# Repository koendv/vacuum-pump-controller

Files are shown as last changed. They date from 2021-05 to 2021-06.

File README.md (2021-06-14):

# vacuum pump controller

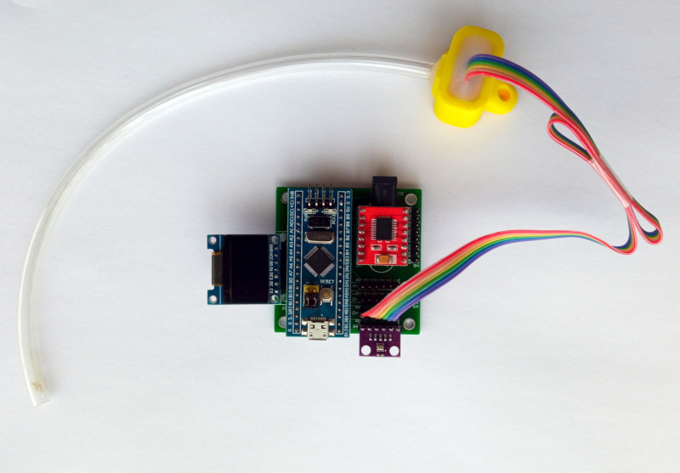
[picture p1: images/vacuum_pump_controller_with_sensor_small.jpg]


This is a controller for a vacuum pump, useful in pick-and-place machines. The controller adjusts the rpm of a vacuum pump to maintain a constant vacuum. The controller can be used over usb, as part of a pick-and-place machine, or standalone, with a footswitch.

## Features:

- PID controller with autotuning

- controls one 12V 1A vacuum pump (diaphragm pump).

- up to 4 x BMP280 pressure sensors: 1 for outside pressure, 1 for vacuum pressure, and 2 for two pick-and-place nozzles. The pressure sensors on the nozzles are used to check whether a component has been picked up or fallen off.

- sensor pressure range 300 to 1100 hPa

- up to 2 x 12V solenoid valves, for up to two pick-and-place nozzles.

## Usage

The controller needs two power sources: +5V from the usb connector for the electronics, and +12V from the DC jack for the vacuum pump and solenoid valves.

Plug the controller in a usb port, and connect to the usb serial port. On linux, this is ``minicom -D /dev/ttyACM0``

Hit the reset button to see the boot message:

```
vacuum controller - type h for help
sensors ok  ok  -  -
ready
>
```
The ``sensors`` line indicates sensor status:

- ``ok`` sensor detected and running
- ``-`` no sensor detected
- ``?`` bmp280 unresponsive, or sensor is wrong type (not bmp280)

Every command is briefly described.

#### h - Help

 ``h`` *help* prints a command summary:

```
>h
commands, ## = int, #.## = float:
? print status
s#.## setpoint
p#.## proportional gain
i#.## integral gain
d#.## derivative gain
o#.## manual mode
a autotune
l## logging on/off
m## m-code
v## valve on/off
w write settings
r reset
f firmware
h help
>
```

All commands are a single character, optionally followed by a number, and terminated with *enter*.

#### ? - print status

```
>?
vacuum hPa: 99.97 motor: 73.60% mode: auto
setpoint hPa: 100.00 Kp: 150.00 Ki: 50.00 Kd: 0.00 logging: 0
pressure hPa: 938.86 838.89 939.41 0.00
sensors ok  ok  ok  -
```
In this example, the boot message shows there are three sensors. The first sensor measures atmospheric pressure; the second sensor measures the pressure in the vacuum vat; the third measures the pressure at the nozzle. In this example the fourth sensor is absent (-).

The vacuum is the difference between the first and the second sensor. All pressures are in hPa. Atmospheric pressure is around 1000 hPa.

*vacuum* is the PID controller measured value. *motor* is PWM, in percent. *mode* is *auto* when the PID controller sets motor PWM. *mode* is *manual* if motor PWM has been set using the ``o`` command.

The vacuum pump controller is a PID controller. *setpoint* is the
desired value; *Kp*, *Ki* and *Kd* are controller proportional, integral and derivative gain. It is normal for *Kd* to be zero. If *logging* is non-zero, pressure is logged on the console every 0.1s.

*pressure* is the pressure from the four sensors, in hPa. If a sensor is not plugged in, the pressure is 0.

*sensors* is the sensor state. If a sensor says ``?``, check the cable, check the sensor is plugged in right, or try power cycling.

#### s - Setpoint

The *setpoint* command sets the desired vacuum, in hPa.
```
>s100.0
ok
```

#### p - Proportional Gain

Sets the PID controller Kp.
```
>p150.0
ok
```

#### i - Integral Gain

Sets the PID controller Ki.
```
>i50.0
ok
```

#### d - Derivative Gain

Sets the PID controller Kd. Usually zero.

```
>d0
ok
```

#### l - Logging

Switches logging on or off.

- ``l0`` logging off.
- ``l1`` logging on.

Use the ``w`` command if you want this and other settings to be saved.

When logging is on, every sample is printed on the console output, in one line, e.g.:
```
;1743075;52417;93876;83764;93926;0;2067058
```
The fields are:
- time since boot in milliseconds
- motor PWM; a value from 0 to 65535.
- pressure of sensor 1, 2, 3, 4 in Pa.
- a checksum that is the 32 bit sum of the 6 previous numbers.

Logging output can be imported in a spreadsheet as [csv](https://en.wikipedia.org/wiki/Comma-separated_values). The line begins with a semi-colon ";", and numbers are separated by a semi-colon. If you parse console output, check for lines that begin with a semi-colon.

#### v - Valve

Switches outputs BO1 and BO2 on/off. These outputs are normally connected to solenoid valves.

- ``v00`` switch BO1 off
- ``v01`` switch BO1 on
- ``v10`` switch BO2 off
- ``v11`` switch BO2 on

*Restriction*: Because of the way the driver ic works, both solenoid valves can not be powered at the same time. Switching one solenoid valve on automatically switches off the other.

#### o - manual Output

Sets the motor PWM manually. Value is a number from 0 to 100, inclusive.

- ``o100`` full speed
- ``o0`` stop. mnemonic: *output zero*
- ``o`` return to automatic mode

#### a - Autotune

*Autotune* measures the step response. Values for Kp, Ki and Kd are calculated from the step response using [lambda tuning](https://www.controleng.com/articles/fundamentals-of-lambda-tuning/). Running *autotune* optimizes controller response time, and the accuracy with which the vacuum is maintained.

```
>a
autotune - press c to cancel
cycle 1/5
  0%    0 hPa
 11%    1 hPa
100%  131 hPa
  0%    0 hPa
100%   83 hPa
minpwm: 7141 maxpwm: 65535 minpressure: 0.49 maxpressure: 130.83
tau: 2.69s Kp: 149.34 Ki: 55.54
...
Kp: 149.60 Ki: 54.03 Kd: 0.00
enter w to save
```

After *autotune*, if the calculated settings seem correct, use ``w`` to store these settings in non-volatile memory. If you choose not to save, the old settings will be restored after the next reset or power cycle.

To adjust the controller to your system, *you need to run autotune* ``a`` *and save the settings* ``w`` *at least once.* Without autotune, controller response will be sluggish.

Run *autotune* again if firmware has been updated, vacuum pump or vacuum vessel has changed.

#### m - M-Code

M-code commands consist of the letter ``M`` followed by a three-digit number. M-code commands are not echoed back when you type them, and no ``>`` prompt is printed when the command is finished. See the section on [OpenPnP](#openpnp) for details.

#### w - Write
The ``w`` write command saves Kp, Ki, Kd, setpoint, and logging to non-volatile memory. The saved values will be restored on power-up.

```
>w
ok
```

#### r - Reset
The ``r`` reset command reboots the controller.

```
>r
vacuum controller - type h for help
sensors ok  ok  ok  -
ready
>
```

#### f - Firmware
The ``f`` command prints firmware version, system uptime, memory and cpu statistics:

```
>f
compiled Jun  1 2021
up 0:16
11240 bytes free
11 ms slowest loop
>
```

Use this to check for reboots, memory leaks, and cpu hogs.

### Connections

Connect pressure sensors, vacuum pump, and solenoid valve.

#### Sensors

Up to 4 BMP280 boards can be connected in headers H1..H4.

- H1: air pressure
- H2: pressure inside vacuum vessel
- H3: optional, pressure at nozzle 1
- H4: optional, pressure at nozzle 2

The minimal configuration is sensors at H1 and H2.
BMP280 sensors measure pressures from 300 hPa to 1100 hPa.

#### Calibration

There is no need to calibrate the sensors; the sensors are calibrated at the factory.

#### Vacuum Pump
 Connect a 12V DC brushless vacuum pump. Maximum current of the TB6612 driver is 1A continuous.

 If the vacuum pump has two wires:

 - red (+) to AO1
 - black (-) to GND

The  vacuum pump is limited to 12V 1A.

For 12V pumps that draw more than 1A, see [pumps with PWM input](README_DEVELOPER.md#pumps-with-pwm-input)

For the controller to work, if the voltage on pin AOUT1 increases, the vacuum pump should run faster, and the vacuum should increase.

#### Solenoid valve

Connect the first solenoid valve:

 - red (+) to B01
 - black (-) to GND

If there is a second solenoid valve, connect:

 - red (+) to B02
 - black (-) to GND

### Footswitch

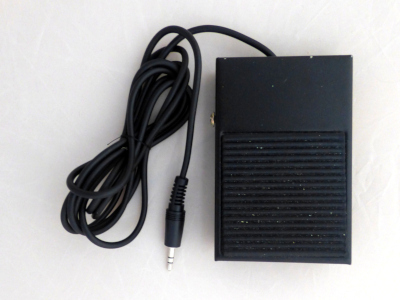
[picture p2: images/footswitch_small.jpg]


Sometimes a small, standalone tool is preferred. The optional footswitch can be used to switch the first solenoid valve on and off.

The footswitch connects using a 3.5mm TRRS jack. Solder a cable from an old mobile phone earset to an [SPDT footswitch](https://www.aliexpress.com/wholesale?SearchText=footswitch&SortType=price_asc). Connections are:

- Tip: NO Normally open
- Ring1: NC Normally closed
- Ring2: unused
- Shield: Common

The console prints ``footswitch`` when a footswitch is detected.

In standalone mode connect the usb port to a mobile phone charger.

## Display

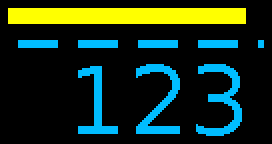
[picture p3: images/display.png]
oled


The display is a yellow/blue oled display, 128x64, SPI, SSD1306 controller. The display is optional; the controller also works without display. The display shows pump, sensors, and vacuum:

- The bargraph at the top shows the pump motor. The larger the bar graph, the harder the motor works.

- Next up to four rectangles, one for each sensor that is plugged in. If the rectangle is blue, the sensor is ok; if the rectangle is yellow there is a problem.

- At the bottom the vacuum in hPa. The vacuum is the difference between the first and the second sensor.

To the right there is a small square that blinks slowly to show the display works.

## Configuration
### linux

On linux, configure udev. As root:

```
cat <<EOD > /etc/udev/rules.d/98-vacuum_pump.rules
ATTRS{idProduct}=="5740", ATTRS{idVendor}=="0483", ENV{ID_MODEL}=="vacuum_pump", MODE="664", GROUP="dialout", ENV{ID_MM_DEVICE_IGNORE}="1"
SUBSYSTEM=="tty", ACTION=="add", ENV{ID_MODEL}=="vacuum_pump", SYMLINK+="ttyACM99_vacuum_pump"
EOD
chmod 644 /etc/udev/rules.d/98-vacuum_pump.rules
udevadm control --reload-rules
```
This creates a device ``/dev/ttyACM99_vacuum_pump``, open to everybody in the *dialout* group. Add yourself to the dialout group:
```
sudo adduser "$USER" dialout
```
Unplug and plug in the vacuum pump controller. Check ``dmesg`` shows a new usb device *vacuum pump*. Check ``minicom -D /dev/ttyACM99_vacuum_pump`` gives you the console prompt of the vacuum pump.

### OpenPnP

*TBD - in progress*

[OpenPnP](https://openpnp.org/) is software to run a machine that puts electronic components on a printed circuit board for soldering (pick-and-place machine).
Typically, a pick-and-place machine uses vacuum to pick up small components.
OpenPnP accesses the vacuum pump controller using the OpenPnP GCodeDriver.

OpenPnP uses M-code M115 to detect a controller.

The m-codes for vacuum have the structure ``M8`` *index* *action*, with *index*:

- 0: ambient air (read only)
- 1: vacuum pump
- 2: nozzle1
- 3: nozzle2

and *action*:

- 0: switch off
- 1: switch on
- 2: read absolute pressure in hPa
- 3: read vacuum in hPa

The following m-codes are available for easy integration with [openpnp](http://openpnp.org):

| code | description |
| ---- | --- |
| M115 | firmware version |
| M800 | no-op |
| M801 | no-op |
| M802 | read absolute air pressure |
| M803 | always reads 0 |
| M810 | switch pump off |
| M811 | switch pump on |
| M812 | read absolute pressure at pump |
| M813 | read vacuum at pump |
| M820 | switch nozzle 1 solenoid off |
| M821 | switch nozzle 1 solenoid on |
| M822 | read absolute pressure at nozzle1 |
| M823 | read vacuum at nozzle1 |
| M830 | switch nozzle 2 solenoid off |
| M831 | switch nozzle 2 solenoid on |
| M832 | read absolute pressure at nozzle2 |
| M833 | read vacuum at nozzle2 |

Example:
Switch pump on.

```
m811
ok
```
Measure absolute air pressure and absolute pump pressure:

```
m802
[read:937]
ok
m812
[read:837]
ok
```
Vacuum is difference between air pressure and pump pressure:

```
m813
[read:100]
ok
```

Vacuum values can be negative due to small measurement errors, or if the sensor for measuring atmospheric pressure is missing.

In OpenPnP, configure a GCodeDriver VACUUM_PUMP for serial port ``/dev/ttyACM99_vacuum_pump``.

Setting|value
---|---
FIRMWARE_NAME|vacuum pump
COMMAND_CONFIRM_REGEX|^ok$
COMMAND_ERROR_REGEX|^(what\\?\|how\\?)$
ACTUATE_BOOLEAN_COMMAND|M8\{Index\}\{True:1\}\{False:0\}
ACTUATOR_READ_COMMAND|M8\{Index\}3
ACTUATOR_READ_REGEX|\\[read:(?<Value>-?\d+)\\]

For head, nozzle 1 and nozzle 2, use three VACUUM_PUMP actuators with index:

Actuator|Index
---|---
head|1
nozzle 1|2
nozzle 2|3

See [machine.xml](openpnp/machine.xml)

## Hardware

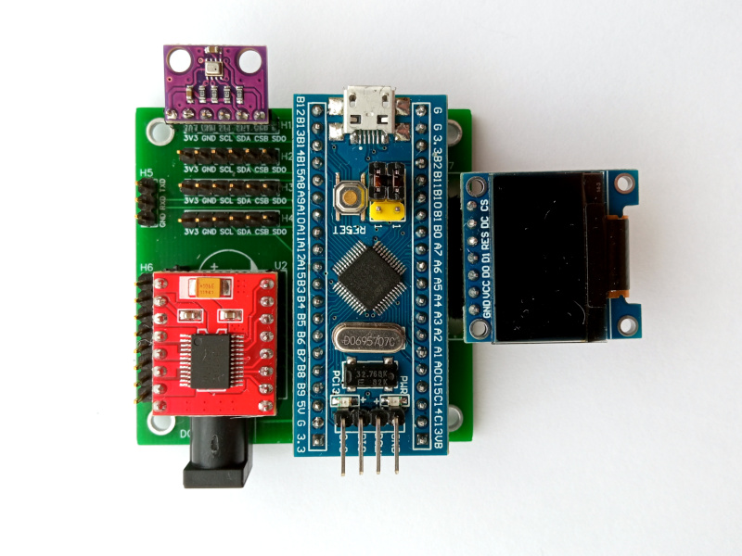
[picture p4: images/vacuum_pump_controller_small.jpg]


The board is built around an STM32F103 *Blue Pill*. The microcontroller reads the pressure from the BMP280 sensors, runs a PID controller algorithm, and sets PWM on a TB6612FNG driver to control the speed of the vacuum pump.

- [schematic](doc/schematic.pdf)
- [pcb top](doc/pcb_top.pdf)
- [pcb bottom](doc/pcb_bottom.pdf)
- [easyeda/oshw project](https://oshwlab.com/koendv/vacuum-pump-controller).

The board is 2 layer, 55 x 55 mm, hand-solderable.

### Bill of Materials

Off-the-shelf parts:

|  #  | description |
| --- | --- |
| 1 | [STM32F103xx](https://www.aliexpress.com/item/32525208361.html) controller board, 128kbyte flash. |
| 4 | [BMP280 3.3V pressure sensor "GY-BMP280-3.3"](https://www.aliexpress.com/item/4000587263474.html) |
| 1 | [TB6612FNG dual motor driver](https://www.aliexpress.com/item/32978024026.html) |
| 1 | [OLED 128x64, SPI, 7pin, SSD1306, yellow/blue](https://www.aliexpress.com/item/32638662748.html)  |
| 1 | DC005 DC jack |
| 1 | PJ-320A 3.5 mm audio jack, 4 pin, through-hole |
| 1 | 47u/25V capacitor |

FDM 3D-printed parts:

- 3 x pressure sensor housing

## Sensors

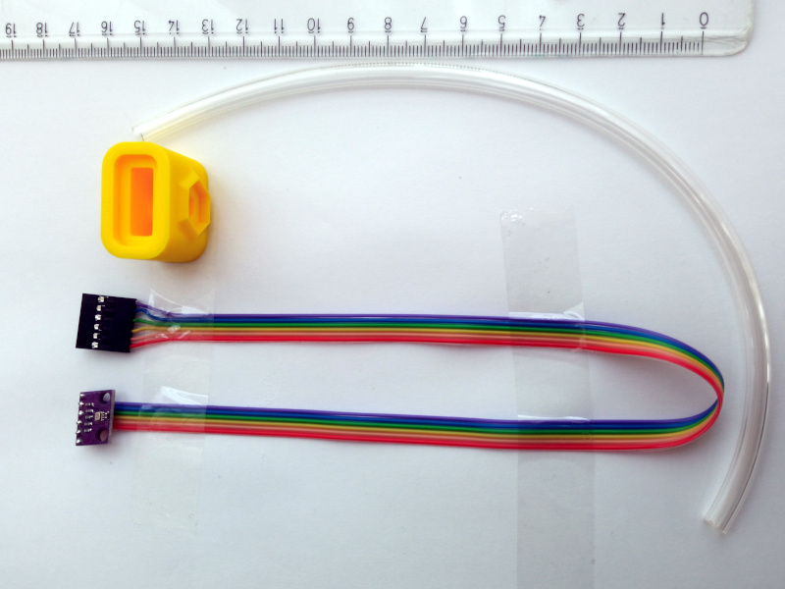
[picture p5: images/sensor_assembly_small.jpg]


The pressure sensor consists of a GY-BMP280-3.3 module, sealed inside a 3d-printed housing.

The housing has been designed using OpenSCAD. [OpenSCAD sources and STL files](openscad/).

The tube is 6mm outside diameter, 4 mm inside diameter PU. Housing is sealed using silicone rubber. After applying the silicone rubber, wet your finger in liquid dishwasher detergent to gently push the silicone rubber into shape.

Test the sensor works *before* you seal the housing.

When looking at the GY-BMP280-3.3 pressure sensor module, the contacts are, from left to right: SDO, CSB, SDA, SCL, GND, VCC.

## Software

The software is an Arduino sketch, compiled with the STM32duino board support package. Sources are available on [git](https://github.com/koendv/vacuum-pump-controller/tree/main/arduino/vacuumcontroller). There's also a backup of the Arduino libraries used.

## Firmware

You can compile and upload the firmware from the Arduino IDE, or use the pre-compiled binaries and upload from the command line. To upload the firmware:

- connect a usb-serial converter to header H5, pins GND, TXD, RXD.
- set Blue Pill jumper BOOT0 to 1, BOOT1 to 0.
- reset or power cycle the Blue Pill
- upload the firmware.
    - If using the Arduino IDE, choose *Sketch->Upload*.
    - If uploading from the command line, use ```/usr/bin/stm32flash -g 0x8000000 -b 115200 -w vacuumcontroller.ino.bin /dev/ttyUSB0```, replacing USB0 with the device of the usb-serial converter.
- set Blue Pill jumper BOOT0 to 0, BOOT1 to 0.
- reset or power cycle the Blue Pill

With the firmware installed, led of the Blue Pill flashes briefly every 5 seconds. The console of the vacuum controller appears as a usb serial port, on linux typically ``/dev/ttyACM0``. If an oled display is attached, the display lights up.

## Download

Download Gerbers for pcb manufacturing, stl files for 3d printing, and firmware for the microcontroller from [releases](releases). Pcb 's ordered at [jlcpcb.com](https://jlcpcb.com/) or [oshpark](https://oshpark.com/shared_projects/RhzQyJqY).

If you like this, maybe you want to buy me a cup of tea:

ko-fi (https://ko-fi.com/Q5Q03LPDQ)

## About

This project was designed on a Raspberry Pi. The electronics pcb was designed using [easyeda](https://oshwlab.com/koendv/vacuum-pump-controller). The arduino sketch was compiled on Raspberry Pi with the [Arduino IDE](https://github.com/koendv/arduino-ide-raspberrypi) using the [stm32duino](https://github.com/koendv/Arduino_Tools) package.  The sensor housing was designed on Raspberry Pi using [OpenSCAD with 3D glasses](https://github.com/koendv/openscad-raspberrypi).

## Links

- [oshw project page](https://oshwlab.com/koendv/vacuum-pump-controller)
- [developer notes](README_DEVELOPER.md)

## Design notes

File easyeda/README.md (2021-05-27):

This is a backup of the project at [easyeda](https://easyeda.com/koendv/vacuum-pump-controller).

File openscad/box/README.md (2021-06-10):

# Box
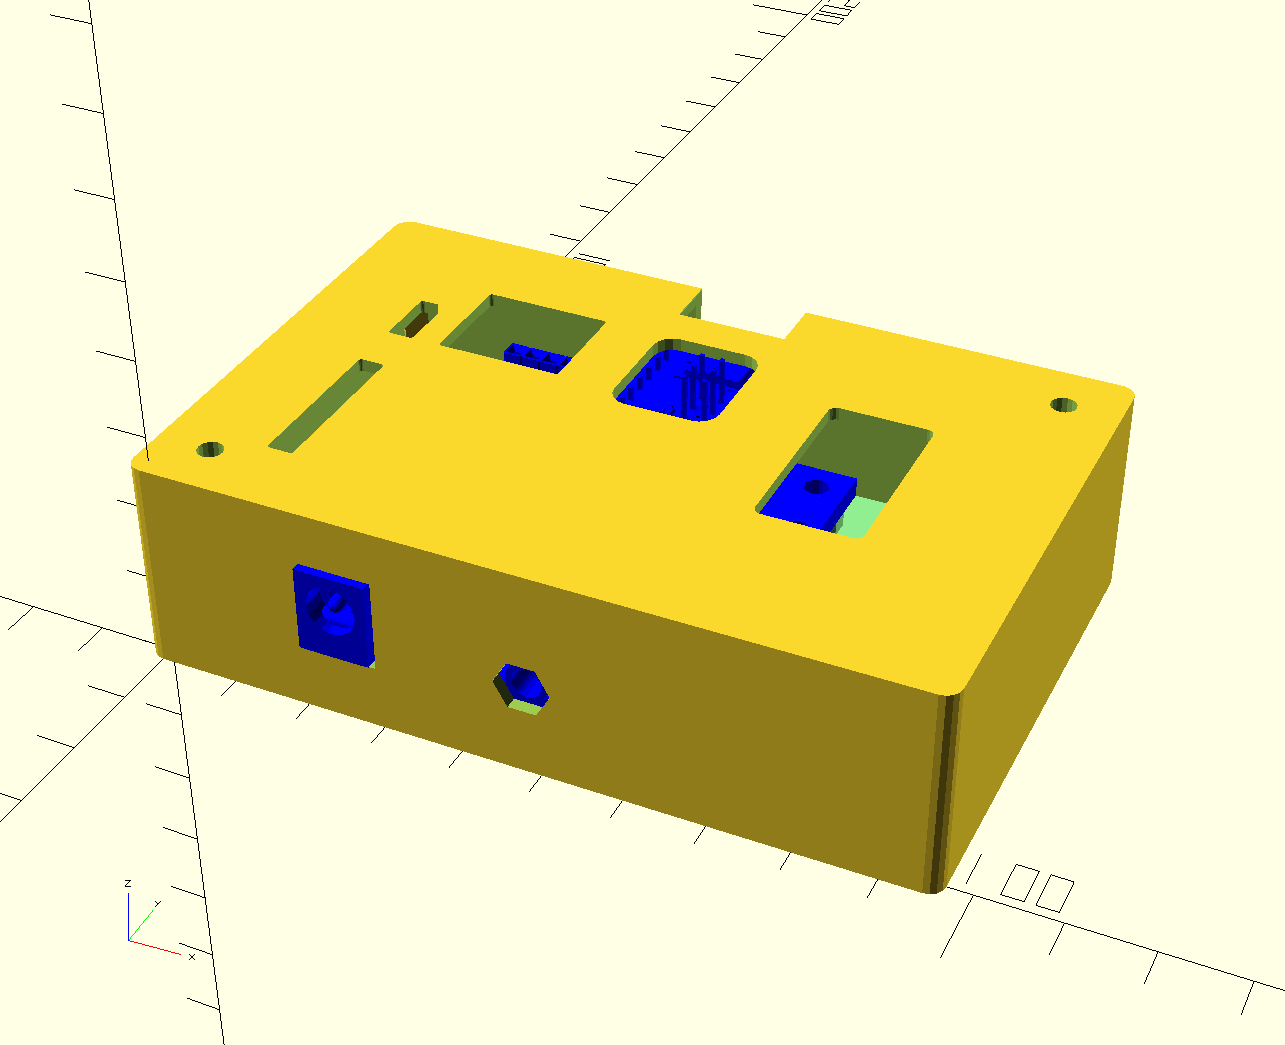
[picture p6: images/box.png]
box enclosure


Box for vacuum pump controller. Print the files [box_top.stl](box_top.stl) and [box_bottom.stl](box_bottom.stl). Ream the screw holes with an M3 wood drill. You can ream by hand: put the drill in a vise, and rotate the workpiece once or twice until the inside of the hole is smooth. Use nylon M3 screws and nuts to join controller pcb, box top and bottom. Snip off screws that are too long.

Small differences exist between different displays. The oled display used has these dimensions:
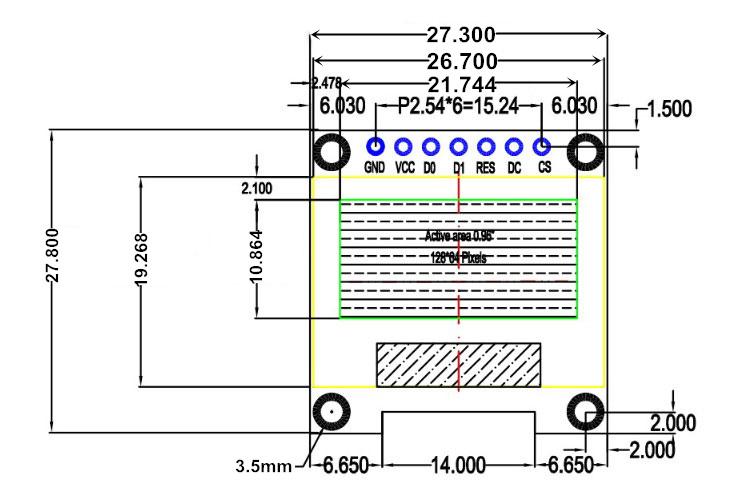
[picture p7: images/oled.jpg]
oled oled 128x64, SSD1306, SPI, 7pin


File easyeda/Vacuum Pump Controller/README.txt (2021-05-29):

<p># Controller for pick-and-place machine vacuum pump.</p>
<p>The controller can be used through usb, as part of a pick-and-place machine, or standalone, with a footswitch.&nbsp;</p>
<p>&nbsp;</p>
<p>## Features</p>
<p>&nbsp;</p>
<p>- up to 4 x BMP280 pressure sensors: 1 for outside pressure, 1 for vacuum pressure, and 2 for two pick-and-place nozzles. The pressure sensors on the nozzles are used to check whether a component has been picked up or has fallen off.&nbsp;</p>
<p>- up to 2 x 12V solenoid valve, one for each pick-and-place nozzle.</p>
<p>&nbsp;</p>
<p>There is an Arduino sketch at <a title="vacuum-pump-controller" href="https://github.com/koendv/vacuum-pump-controller">github</a></p>            
How to use：

At editor, Click the document icon on the topbar, via "Document" > "Open" > "EasyEDA Source", and select json file, then open it at the editor.

如何使用：

在编辑器顶部工具栏，点击“文档”图标，选择 “文档” > “打开” > “EasyEDA源码”，选择json文件打开即可。

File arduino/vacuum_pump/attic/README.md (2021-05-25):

Additional code for a 128x64 oled display with ssd1306 controller, connected via i2c.
connections:
 PIN_SCL PB10
 PIN_SDA PB11

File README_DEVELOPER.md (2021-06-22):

# Developer Notes

## Project goals

Goal is stable, steady vacuum at low cost.

## Software

The software allows hot-plugging the sensors. 

Plugging in a sensor is detected by setting the chip select pin to INPUT_PULLDOWN and reading the pin status. When a sensor is present chip select pin will be pulled high.

A removed sensor is detected by trying to read the chip id over spi, and finding the chip id has changed.

The Adafruit Unified Sensor interface was not used because using getPressure() directly has more precision, and more precision gives smoother PID control.

The software is easily adapted to other BMPxxx sensors.

## Hardware

The electronics have been kept simple, so there is little that can fail. The board can be soldered by hand.

I've experimented plugging and unplugging sensor and display when connecting over i2c and spi. With spi, worst case is the sensor does not work. With i2c, worst case is the system hangs. Because I want long term stability and unattended functioning I used spi *and* configured a watchdog timer.

The sensors do not have a reset pin. If long-term stability is a problem, power the sensors through a AP2112K-3.3 low drop voltage regulator with the voltage regulator enable connected to a processor pin. This way the processor can power cycle the sensors if the sensors need a hard reset.

## Pumps with PWM input
*XXX checkme*

Vacuum pumps with PWM input can be connected like this:

 - red (+) to 12V
 - black (-) to GND
 - PWM input to AO1
 - Tacho output does not need to be connected

The vacuum pump can exceed 1A, as the TB6612 driver only has to supply the PWM signal.

The pump motor PWM input signal has to toggle between low and high impedance. According to the truth table "H-SW Control Function" in the [TB6612 datasheet](doc/TB6612FNG_datasheet_en_20141001.pdf), this can be done with:

 - STBY high
 - PWMA high
 - AIN1 low
 - AIN2 PWM signal

This toggles AOUT1 between L (low) and OFF (high impedance). See [patch](arduino/vacuum_pump/attic/motor_with_pwm_input.patch)

On a Parker D1001-23-01 vacuum pump, wire colors are: red 12V, black ground, white PWM, blue tacho. Check datasheet before connecting.

## Footswitch

The footswitch connector has one digital/analog and two digital contacts. The controller works with a SPDT footswitch.

If you wish to connect an analogue footswitch (like those used on sewing machines) there is source in [footswitch.cpp.analog](arduino/vacuumcontroller/attic/footswitch.cpp.analog)

## Autotuning

Autotuning sets the PID controller gain.

The algorithm used is the following:

- Find the lowest voltage where the pump begins to turn.
Beginning with pressure 0 and pwm 0, slowly increase pwm until pressure increases. Note this data as (minpwm, minpressure).
- Find the steady-state pressure.
Set the motor to full 12V (100% PWM), and wait until pressure no longer increases. Note this data as (maxpwm, maxpressure).
- Draw a line through the two points (minpwm, minpressure) and (maxpwm, maxpressure) and calculate the slope. The PID controller proportional gain is set to the slope, divided by a safety factor 3:



- An exponentially dampened process 
reaches value 0.63 at t = &tau;. Beginning with pressure 0 and pwm 0, set the vacuum pump at full 12V (100% PWM), and measure the time for pressure to reach 63% of steady-state pressure:

This time measurement gives the time constant &tau;. The PID controller integral gain is set at
 


- The PID controller differential gain is set to zero:



The safety factor can be tuned a little to trade off stability for accuracy, if needed.

The step response can be measured by turning on logging ``l1`` and switching between pump off ``o0`` and pump on ``o100``. Capture console output, and import in a spreadsheet as csv. Use as input for PID tuning software.

## Ways to save flash

Simple measures to save flash.

- The sketch uses a 24pt bitmap font to display the vacuum on an oled display. Fonts use a lot of flash memory, especially at larger point sizes. Optimize by storing only those characters actually needed. The font ``Veranda24ptDigits.h`` only contains the characters ``-./01234567890:``, sufficient to print positive and negative integers and floats and the time. Font size is 1223 bytes, a saving of 7643 bytes compared to the full font.

- Disable support for unused Serial1 port. The serial port is only used for initial firmware upload. 
  *Tools -> U(S)ART support -> Disabled (no Serial support)*
  saves 2468 bytes flash

- Remove Adafruit_SSD1306 flash screen.
  This removes the splash screen bitmap from the SSD1306 driver. Saves 1352 bytes flash.
  [patch](arduino/libraries/Adafruit_SSD1306.patch)

- Set "Optimize: Smallest (-Os) with LTO"
  [Link Time Optimization](https://gcc.gnu.org/wiki/LinkTimeOptimization) (LTO) saves 11828 bytes flash. But sometimes LTO drops too much code, so this option requires careful checking the program still works after LTO.

If LTO works, these measures save 23291 bytes flash, enough for the code to fit in 64K. (size: 63756 bytes). Personally, I think it's safer to buy a STM32F013 with 128 kbyte flash, and avoid use of LTO until flash is full.

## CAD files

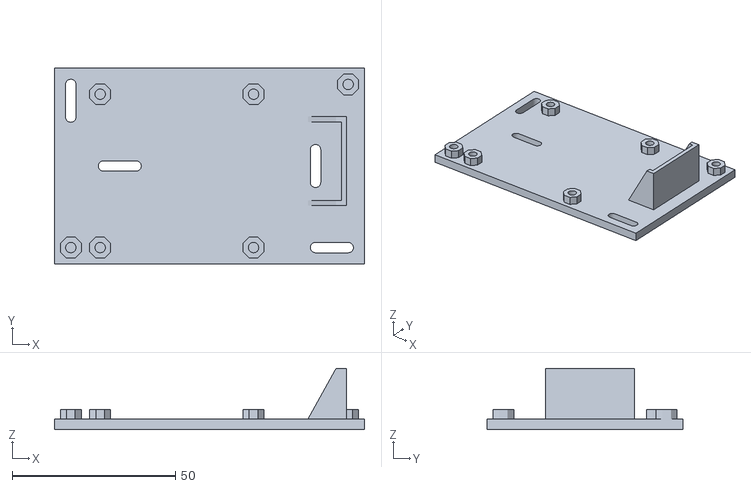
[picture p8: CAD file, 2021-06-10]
openscad/box/box_bottom.stl
95.0 x 60.0 x 18.8

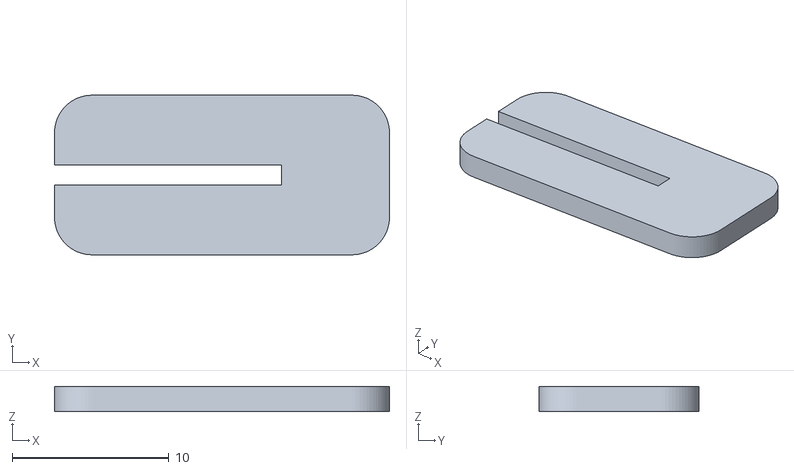
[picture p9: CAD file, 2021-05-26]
openscad/sensor/pressure_sensor_lid.stl
21.4 x 10.2 x 1.60

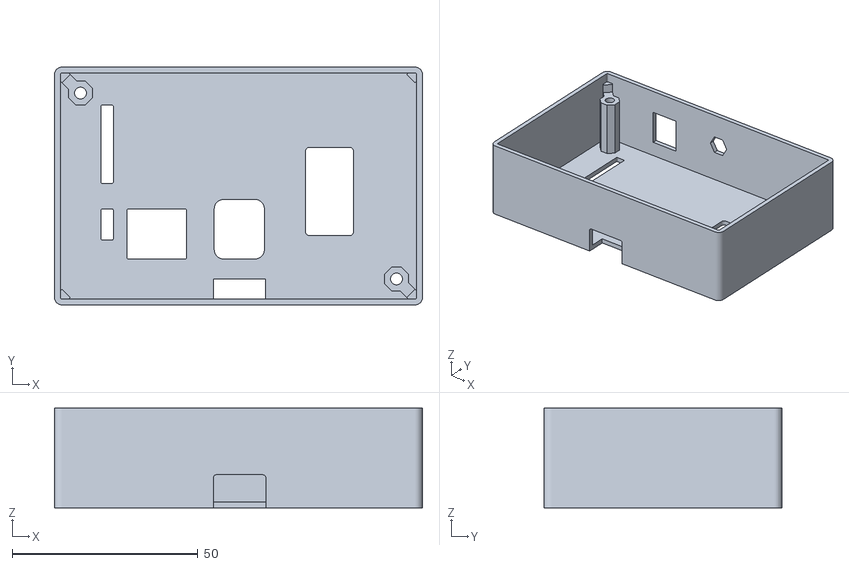
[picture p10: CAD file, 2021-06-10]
openscad/box/box_top.stl
99.0 x 64.0 x 26.8

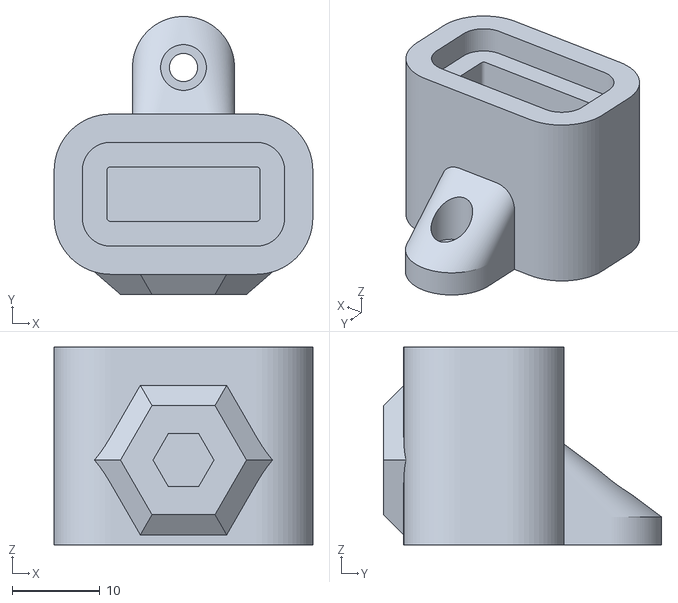
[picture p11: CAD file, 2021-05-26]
openscad/sensor/pressure_sensor.stl
29.4 x 31.6 x 22.5

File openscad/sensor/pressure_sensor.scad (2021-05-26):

/*
 * box for BMP280 pressure sensor modules GY-BMP280-3.3, pcb size 16x12 mm.
 *
 * Slide the sensor module in at the top of the box, pressure sensor
 * facing the hole in the front of the box, connecting cable up.
 * Put 6mm diameter pneumatic tubing in the hole in the front of the box.
 * Put workpiece "lid" on top, with cable through slot in workpiece.
 * Seal top and front with silicon rubber.
 */
include <util.scad>

eps1 = 0.001;
eps2 = 2*eps1;
$fn=$preview ? 32 : 64;
nozzle_size = 0.4;
wall = 3.2;

pcb_x = 15.8+2*nozzle_size;
pcb_z = 12.5+nozzle_size;
pcb_y = 5.0+nozzle_size;

box_z = pcb_z+3*wall;

tube_dia = 6.0;
tube_x = pcb_x/2;
tube_y = -pcb_y/2-wall+nozzle_size;
tube_z = pcb_z/2+wall;

screw_hole = 3.2;
screw_offset = pcb_y/2 + 4*wall + screw_hole/2;
washer_dia = 5.2;

module box() {
    difference() {
        box_body();
        box_holes();
    }
}

module box_body() {

    linear_extrude(box_z)
    offset(2*wall)
    square([pcb_x, pcb_y]);

    /* tab for screw */
    hull() {
        translate([pcb_x/2, 0, screw_offset+wall])
        cube([washer_dia+2*wall, eps1, eps1], center=true);
        linear_extrude(wall)
        offset(wall)
        hull() {
            translate([pcb_x/2, 0, 0])
            square([washer_dia, eps1], center=true);
            translate([pcb_x/2,screw_offset, 0])
            circle(d=washer_dia);
        }
    }

    /* tube */
    tube_body();

}

module box_holes() {
    translate([0,0,wall+pcb_z+wall])
    linear_extrude(pcb_z+2*wall)
    offset(wall)
    square([pcb_x, pcb_y]);

    translate([0,0,wall])
    linear_extrude(pcb_z+2*wall)
    offset(nozzle_size)
    square([pcb_x, pcb_y]);

    translate([pcb_x/2,screw_offset, -pcb_z])
    linear_extrude(2*pcb_z)
    circle(d=screw_hole);

    translate([pcb_x/2,screw_offset, wall])
    linear_extrude(2*pcb_z)
    circle(d=washer_dia);

    tube_hole();

}

module tube_body() {
    translate([tube_x,tube_y,tube_z])
    rotate([90,0,0])
    hull() {
        cylinder_outer(d=tube_dia+2*wall, h=wall, fn=6);
        cylinder_outer(d=tube_dia+4*wall, h=eps1, fn=6);
    }
}

module tube_hole() {
    translate([tube_x,0,tube_z])
    rotate([90,0,0])
    cylinder_outer(d=tube_dia, h=100, fn=6);
    translate([tube_x,tube_y,tube_z])
    rotate([90,0,0])
    cylinder_outer(d=tube_dia+2*wall, h=100, fn=6);
}

module lid() {
    cable_width = 1.27*6;
    cable_thickness = 1.27;
    translate([0,0,0])
    linear_extrude(wall/2)
    difference() {
        offset(wall-2*nozzle_size)
        square([pcb_x, pcb_y]);
        translate([0, pcb_y/2])
        square([pcb_x + cable_width, cable_thickness], center=true);
    }
}

module assembly() {
    box();
    /* tube */
    color("Blue")
    translate([tube_x,tube_y+wall,tube_z])
    rotate([90,0,0])
    difference() {
        cylinder(d = tube_dia, h =20);
        translate([0,0,-eps2])
        cylinder(d = tube_dia/2, h =40);
    }
    /* pcb */
    color("Purple")
    translate([0,0,wall])
    cube([pcb_x, pcb_y, pcb_z]);
    /* lid */
    if (0)
    translate([0,0,wall+pcb_z+wall+eps1])
    lid();
}

assembly();
//box();
//lid();

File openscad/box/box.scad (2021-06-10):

include <pcb.scad>
include <util.scad>

$fn=$preview?16:32;
nozzle_size = 0.4;
wall_thickness = 4 * nozzle_size;
z_inside = 22;
pcb_pillar = 3.0;
pcb_thickness = 1.6;

w = 60;
h = 95;
border = 5;
slot_len = 10;

offset_x = pcb_offset_x+10;
offset_y = pcb_offset_y+1;
offset = [offset_x, offset_y];

m3_screw_d = 3.2;
m3_nut_h = 2.4+nozzle_width;
m3_nut_d = 5.5+nozzle_width;
m3_nut_coords = [
    [offset_x, offset_y, 0],
    [offset_x, offset_y+47, 0],
    [offset_x+47, offset_y, 0],
    [offset_x+47, offset_y+47, 0],
    [border, border, 0],
    [h-border, w-border, 0]
    ];

bottom_thickness = m3_nut_h + nozzle_width;

// oled dimensions from oled.jpg
oled_w = 27.3;
oled_h = 27.8;
oled_x = 21.744;
oled_y = 10.864;
oled_z = bottom_thickness+pcb_pillar+pcb_thickness+11.0;

oled_dist = (27.8 - 19.268)/2 + 2.1 - 1.5; // distance from connector pin to first pixel 

// cutout for oled display
module oled_screen() {
    corner = pins_screws[0];
    pin3 = (pin3_oled-corner) / 1000;
    translate(offset+pin3)
    translate([oled_dist, -oled_x/2])
    offset(1.0)
    square([oled_y, oled_x]);
}

// 8-sided pillar for m3 screw
module m3_pillar() {
    rotate([0, 0, 180/8])
    circle_outer(d=m3_screw_d+2*wall_thickness, fn=8);
}

// circle same diameter as M3 screw
module m3() {
    circle(d=m3_screw_d);
}

module m3_nut_trap() {
    translate([0, 0, -eps2])
    cylinder_outer(d=m3_nut_d, h=m3_nut_h, fn=6);
}

module m3_nut_traps() {
    for (p = m3_nut_coords) {
        translate(p)
        m3_nut_trap();
    }
}

// this is a one layer bridging layer obove the nut trap
// needed for fdm printing
module m3_nut_bridging() {
    translate([0, 0, m3_nut_h])
    for (p = m3_nut_coords) {
        translate(p)
        cylinder(d=m3_nut_d, h=nozzle_width);
    }
}

// screws to join top and bottom
module through_holes() {
    translate([border, border]) m3();
    translate([h-border, w-border]) m3();
}

module top_pillars() {
    translate([0, 0, bottom_thickness + pcb_pillar])
    linear_extrude(z_inside - pcb_pillar) {
        translate([border, border])
        m3_pillar();
        translate([h-border, w-border])
        m3_pillar();
        hull() {
            translate([h, w])
            circle(r=wall_thickness);
            translate([h-border, w-border])
            circle(r=wall_thickness);
        } 
        hull() {
            circle(r=wall_thickness);
            translate([border, border])
            circle(r=wall_thickness);
        }
    }
}

module bottom_pillars() {
    linear_extrude(pcb_pillar+bottom_thickness)
    for (p = m3_nut_coords) {
        translate(p)
        m3_pillar();
    }
}

// slots for wall-mount
module slots() {
    hull() {
        translate([border, w-border]) m3();
        translate([border, w-border-slot_len]) m3();
    }
    hull() {
        translate([h-border, border]) m3();
        translate([h-border-slot_len, border]) m3();
    }
    hull() {
        translate([border+slot_len, w/2]) m3();
        translate([border+2*slot_len, w/2]) m3();
    }
    hull() {
        translate([h-border-slot_len, w/2-slot_len/2]) m3();
        translate([h-border-slot_len, w/2+slot_len/2]) m3();
    }
}

module top_holes() {
    translate(offset)
    pcb_top_holes();
    through_holes();
    oled_screen();
}

module bottom_holes() {
    translate(offset)
    pcb_bottom_holes();
    through_holes();
    slots();
}

module top() {
    difference(){
        top_body();
        linear_extrude(2*z_inside)
        top_holes();
        dc005_jack();
        pj320a_jack();
        usb_connector();
    }
    // small triangular corners
    translate([0, 0, bottom_thickness])
    linear_extrude(z_inside)
    intersection() {
        for (p = [[0,0], [0,w], [h,0], [h,w]]) {
            translate(p)
            rotate([0, 0, 45])
            square([2*wall_thickness, 2*wall_thickness], center=true);
        }
        offset(nozzle_size)
        square([h,w]);
    }
}

module top_body() {
    difference() {
        linear_extrude(bottom_thickness+z_inside+wall_thickness)
        offset(nozzle_size+wall_thickness)
        square([h,w]);
        translate([0, 0, -2*eps2])
        linear_extrude(bottom_thickness+z_inside)
        offset(nozzle_size)
        square([h,w]);
    }
    top_pillars();
}

module bottom() {
    difference() {
        bottom_body();
        translate([0, 0, -bottom_thickness])
        linear_extrude(z_inside)
        bottom_holes();
        m3_nut_traps();
    }
    m3_nut_bridging();
}

module bottom_body() {
    linear_extrude(bottom_thickness)
    square([h,w]);
    // pillars
    bottom_pillars();
    // buttress under oled
    oled_support();
}

module dc005_jack() {
    translate([19.5,-5,bottom_thickness+pcb_pillar+pcb_thickness+nozzle_width])
    cube([9+2*nozzle_width,14.2+2*nozzle_width,11+2*nozzle_width]);
}

module pj320a_jack() {
    translate([47.75,0,bottom_thickness+pcb_pillar+pcb_thickness+3.7])
    rotate([90,0,0])
    cylinder_outer(d=6.1,h=12.9,fn=6);
}

module usb_connector(){
    translate([47.8, 60, 14.8])
    translate([0, 0, bottom_thickness+pcb_pillar+pcb_thickness])
    rotate([90, 0, 0])
    translate([0, 0, -5])
    linear_extrude(10)
    offset(2*nozzle_width)
    //square([8.4, 2.6], center=true); // usb c  connector
    square([12.5, 7.8], center=true); // connector with overmold
}


module oled_support() {
    corner = pins_screws[0];
    pin3 = (pin3_oled-corner) / 1000;
    translate(offset+pin3)
    translate([oled_h, -oled_w/2, 0])
    difference() {
        hull() {
            translate([-2*wall_thickness,0,0])
            cube([2*wall_thickness, oled_w, oled_z]);
            translate([-oled_w/2,0,0])
            cube([oled_w/2, oled_w, eps]);
        }
        translate([-oled_w-wall_thickness, wall_thickness, -eps])
        cube([oled_w,oled_w-2*wall_thickness,2*oled_z]);
    }
}

// 3d model
module 3d_model() {
    color("Blue")
    translate([39.3,28.2,bottom_thickness+pcb_pillar+8.1]) // trial and error
    scale(0.254)
    translate([-4166.994629,3158.121338,-31.578953]) // from meshlab, Filters -> Quality measures and computations -> Compute Geometric Measures
    import("vpc.stl", 20); // exported from easyeda
}

if (1)
translate([0, 0, eps])
//rotate([180,0,0])
top();
if (1)
color("LightGreen")
bottom();
if (0)
3d_model();

//not truncated

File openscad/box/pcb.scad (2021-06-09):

// This file contains the coordinates of the pcb pins. 
// The pin coordinates were determined like this:

// Open the pcb in easyeda. Set units to mm.
// Generate Gerbers.  
// Join the files Gerber_Drill_NPTH.DRL and Gerber_Drill_PTH.DRL.
// The header will look similar to this:
//
// METRIC,LZ,000.000

// Edit the Gerber file:
// replace X with [
// replace Y with ,
// replace eol with ],
// replace G85 with ],
// So a line like this
// X045705Y048914
// becomes this:
// [045705,048914],
// and paste the result in this openscad script.

// pins1 is the pin coordinates, as found in the gerber files
pins1 = [
  [045705,048914],
  [045644,055932],
  [038100,099060],
  [038100,096520],
  [038100,093980],
  [038100,091440],
  [038100,088900],
  [038100,086360],
  [038100,083820],
  [038100,081280],
  [038100,078740],
  [038100,076200],
  [038100,073660],
  [038100,071120],
  [038100,068580],
  [038100,066040],
  [038100,063500],
  [038100,060960],
  [038100,058420],
  [038100,055880],
  [038100,053340],
  [038100,050800],
  [053340,099060],
  [053340,096520],
  [053340,093980],
  [053340,091440],
  [053340,088900],
  [053340,086360],
  [053340,083820],
  [053340,081280],
  [053340,078740],
  [053340,076200],
  [053340,073660],
  [053340,071120],
  [053340,068580],
  [053340,066040],
  [053340,063500],
  [053340,060960],
  [053340,058420],
  [053340,055880],
  [053340,053340],
  [053340,050800],
  [010160,088900],
  [010160,086360],
  [017145,099060],
  [019685,099060],
  [022225,099060],
  [024765,099060],
  [027305,099060],
  [029845,099060],
  [017145,083820],
  [019685,083820],
  [022225,083820],
  [024765,083820],
  [027305,083820],
  [029845,083820],
  [017145,088900],
  [019685,088900],
  [022225,088900],
  [024765,088900],
  [027305,088900],
  [029845,088900],
  [017145,093980],
  [019685,093980],
  [022225,093980],
  [024765,093980],
  [027305,093980],
  [029845,093980],
  [010160,073660],
  [010160,071120],
  [010160,068580],
  [010160,066040],
  [010160,063500],
  [010160,060960],
  [010160,058420],
  [010160,055880],
  [043515,058230],[043515,057330],
  [047925,059229],[047925,058329],
  [043515,054230],[043515,053330],
  [043515,050891],[043515,049991],
  [059690,069850],
  [059690,072390],
  [059690,074930],
  [059690,077470],
  [059690,080010],
  [059690,082550],
  [059690,085090],
  [020320,073660],
  [025400,073660],
  [010160,083820],
  [030480,073660],
  [030480,071120],
  [030480,068580],
  [030480,066040],
  [030480,063500],
  [030480,060960],
  [030480,058420],
  [030480,055880],
  [015240,055880],
  [015240,058420],
  [015240,060960],
  [015240,063500],
  [015240,066040],
  [015240,068580],
  [015240,071120],
  [015240,073660],
  [023465,050975],[021265,050975],
  [023465,056975],[021265,056975],
  [027165,055575],[027165,053375],
  [012000,051000],
  [012000,098000],
  [059000,098000],
  [059000,051000],
];
  
// following coordinates have been extracted from pins1[]:

pins_screws = [  
  [012000,051000],
  [012000,098000],
  [059000,098000],
  [059000,051000],
];

pins_stm32 = [
//  [045705,048914],
//  [045644,055932],
//  [038100,099060],
  [038100,096520],
  [038100,093980],
  [038100,091440],
  [038100,088900],
  [038100,086360],
  [038100,083820],
  [038100,081280],
  [038100,078740],
//  [038100,076200],
//  [038100,073660],
//  [038100,071120],
//  [038100,068580],
//  [038100,066040],
//  [038100,063500],
//  [038100,060960],
//  [038100,058420],
//  [038100,055880],
//  [038100,053340],
//  [038100,050800],
//  [053340,099060],
  [053340,096520],
  [053340,093980],
  [053340,091440],
  [053340,088900],
  [053340,086360],
  [053340,083820],
  [053340,081280],
  [053340,078740],
//  [053340,076200],
//  [053340,073660],
//  [053340,071120],
//  [053340,068580],
//  [053340,066040],
//  [053340,063500],
//  [053340,060960],
//  [053340,058420],
//  [053340,055880],
//  [053340,053340],
//  [053340,050800],
];

pins_sensors = [
//  [017145,099060],
//  [019685,099060],
//  [022225,099060],
//  [024765,099060],
//  [027305,099060],
//  [029845,099060],
  [017145,083820],
  [019685,083820],
  [022225,083820],
  [024765,083820],
  [027305,083820],
  [029845,083820],
  [017145,088900],
  [019685,088900],
  [022225,088900],
  [024765,088900],
  [027305,088900],
  [029845,088900],
  [017145,093980],
  [019685,093980],
  [022225,093980],
  [024765,093980],
  [027305,093980],
  [029845,093980],
  ];
  
pins_serial = [
  [010160,088900],
  [010160,086360],
  [010160,083820],
  ];

pins_motor = [  
  [010160,073660],
  [010160,071120],
  [010160,068580],
  [010160,066040],
  [010160,063500],
  [010160,060960],
  [010160,058420],
  [010160,055880],
  ];

// pin3 of the oled - the pin in the middle
pin3_oled = [059690,077470];

pcb_x = 55.0;
pcb_y = 55.0;
pcb_offset_x = (55.0-47.0)/2;
pcb_offset_y = (55.0-47.0)/2;

$fn = $preview?16:64;
inch = 25.4;
nozzle_width = 0.4;
eps = 0.001;
eps2 = 2*eps;

module pin(x,dia) {
    translate(x)
    cylinder(h=1, d=dia);
}

module dupont_pin(x) {
    translate(x)
    square([inch/10, inch/10], center=true);
}

module dupont_connector(xarray) {
    corner=pins_screws[0];
    offset(nozzle_width)
    hull()
    for (p1 = xarray) {
        p1=(p1-corner)/1000;
        dupont_pin(p1);
    }
}

module pcb_allholes() {
    corner=pins_screws[0];
    for (p1 = pins1) {
        p1=(p1-corner)/1000;
        translate(p1)
        circle(d=1);
    }
}

module screw_holes() {
    corner=pins_screws[0];
    for (p1 = pins_screws) {
        p1=(p1-corner)/1000;
        translate(p1)
        circle(d=3.2);
    }
}
module stm32_button_and_jumpers() {
    offset(inch/10)
    offset(-2*inch/10)
    hull()
    dupont_connector(pins_stm32);
}

module pcb_top_holes() {
    dupont_connector(pins_serial);
    dupont_connector(pins_motor);
    dupont_connector(pins_sensors);
    stm32_button_and_jumpers();
    //screw_holes();
}

module pcb_bottom_holes() {
    screw_holes();
}

module pcb_board() {
    translate([-pcb_offset_x, -pcb_offset_y])
    square([pcb_x, pcb_y]);
}

module pcb() {
    color("Black")
    translate([0, 0, 2*eps])
    pcb_allholes();
    color("Red")
    translate([0, 0, eps])
    pcb_top_holes();
    color("Blue")
    translate([0, 0, eps])
    pcb_bottom_holes();
    color("Green")
    pcb_board();
}


//pcb();

// not truncated

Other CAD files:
openscad/box/util.scad

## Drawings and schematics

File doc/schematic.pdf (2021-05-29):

## Firmware upload USB Serial Converter

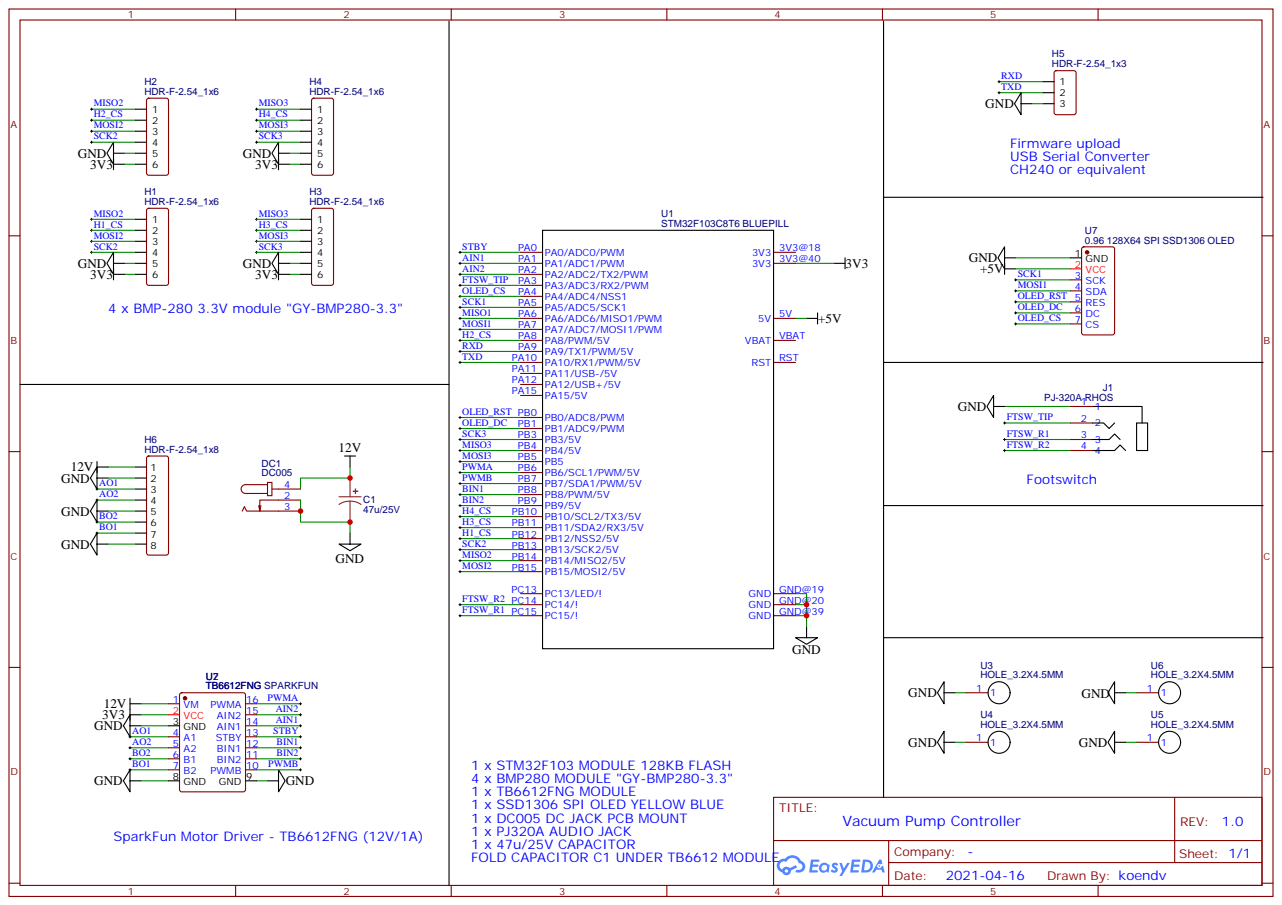
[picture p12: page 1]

PA0/ADC0/PWM PA0
PA15/5V PA15 PA12/USB+/5V PA12 PA11/USB-/5V PA11 PA10/RX1/PWM/5V PA10 PA9/TX1/PWM/5V PA9 PA8/PWM/5V PA8 PA7/ADC7/MOSI1/PWM PA7 PA6/ADC6/MISO1/PWM PA6 PA5/ADC5/SCK1 PA5 PA4/ADC4/NSS1 PA4 PA3/ADC3/RX2/PWM PA3 PA2/ADC2/TX2/PWM PA2 PA1/ADC1/PWM PA1

PB15/MOSI2/5V PB15 PB14/MISO2/5V PB14 PB13/SCK2/5V PB13 PB12/NSS2/5V PB12 PB11/SDA2/RX3/5V PB11 PB10/SCL2/TX3/5V PB10 PB9/5V PB9 PB8/PWM/5V PB8 PB7/SDA1/PWM/5V PB7 PB6/SCL1/PWM/5V PB6 PB5 PB5 PB4/5V PB4 PB3/5V PB3 PB1/ADC9/PWM PB1 PB0/ADC8/PWM PB0

1 x STM32F103 MODULE 128KB FLASH
4 x BMP280 MODULE "GY-BMP280-3.3"
1 x TB6612FNG MODULE
1 x SSD1306 SPI OLED YELLOW BLUE
1 x DC005 DC JACK PCB MOUNT
1 x PJ320A AUDIO JACK
1 x 47u/25V CAPACITOR
FOLD CAPACITOR C1 UNDER TB6612 MODULE

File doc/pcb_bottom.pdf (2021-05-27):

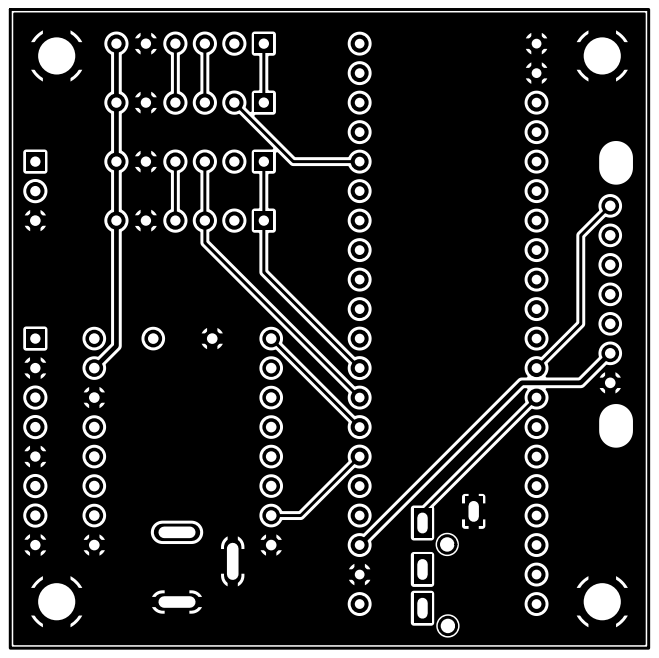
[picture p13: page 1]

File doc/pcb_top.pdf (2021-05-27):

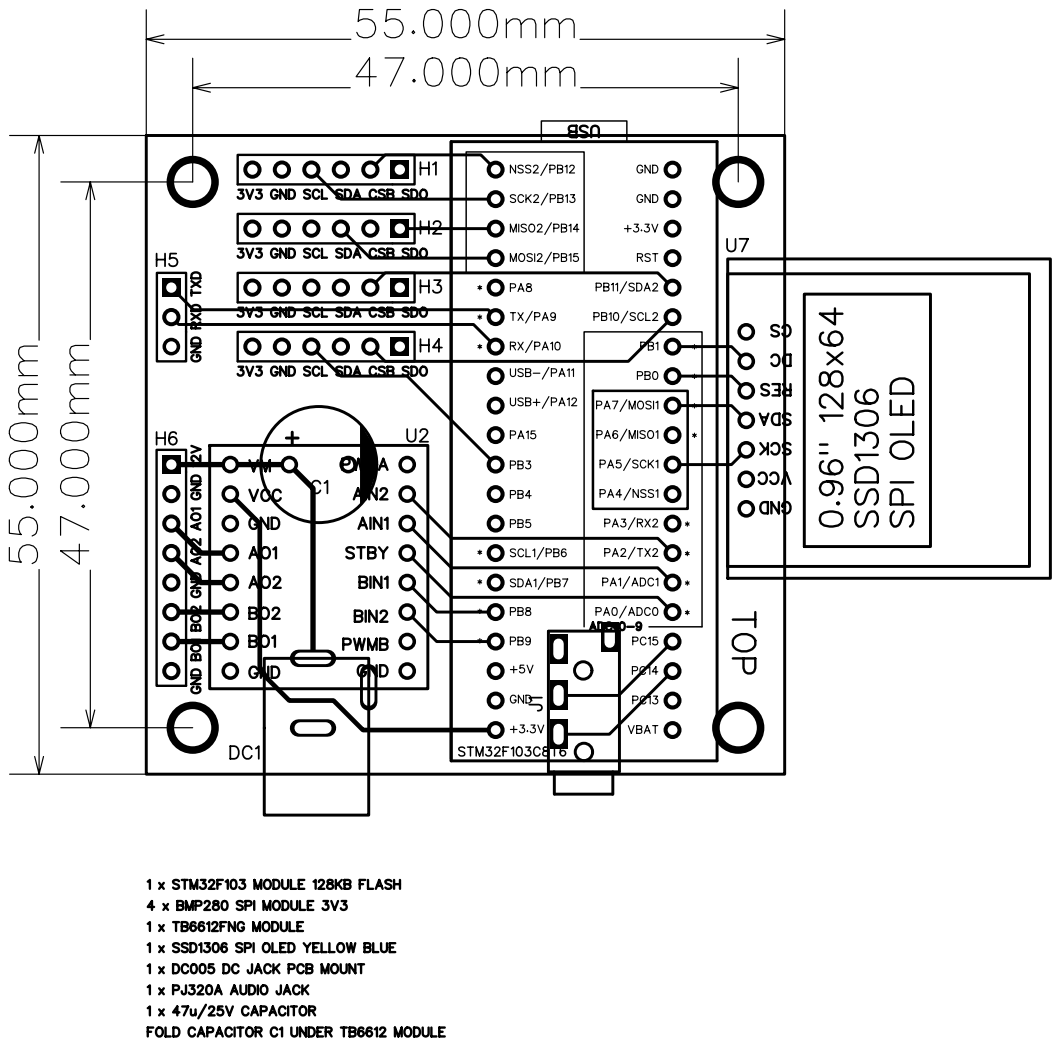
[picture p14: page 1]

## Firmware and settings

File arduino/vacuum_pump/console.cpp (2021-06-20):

#include "console.h"
#include "autotune.h"
#include "bytesfree.h"
#include "display.h"
#include "loopstats.h"
#include "motor.h"
#include "pidctrl.h"
#include "sensor.h"
#include "settings.h"
#include "uptime.h"
#include "watchdog.h"
#include <Arduino.h>

#define MAXCMDLEN 64

/* console command line interpreter.
 * A command is a character, optionally followed by an integer or floating-point number.
 * Status messages are:
 * "init"  - non-volatile storage reset to defaults
 * "ok"    - command successful
 * "how?"  - illegal value
 * "what?" - syntax error
 *
 * To stop pressure being logged to the console, enter 'l0'.
 */

namespace console {

enum err_code { ERR_OK,
                ERR_SYNTAX,
                ERR_VALUE };
enum err_code ok = ERR_OK;
bool echo_on = true;

String cmdline;

void reset() {
  Serial.println("ok");
  Serial.flush();
  motor::speed(0);
  motor::setswitch(2, false);
  motor::setswitch(3, false);
  watchdog::reboot();
}

// m-codes, for easy compatibility with openpnp.org

// print sensor s pressure in hPa as m-code response
void m_pressure(int m, int s, bool relative) {
  int32_t p;
  sensor::readSensors();
  p = sensor::ipressure[s]; // pressure in Pa
  if (relative) {
    // vacuum can be negative due to small measurement errors,
    // or if the sensor for measuring atmospheric pressure is missing.
    p = sensor::ipressure[0] - p; // relative vacuum
  }
  p = p / 100; // convert from Pa to hPa
  Serial.print("[read:");
  Serial.print(p);
  Serial.println(']');
}

// parse m-code

// m-code format: M8 sensor_number action
// where:
//   sensor_number 0=air, 1=pump, 2=nozzle1, 3=nozzle2
//   action 0=off, 1=on, 2=read absolute pressure in hPa, 3=read vacuum in hPa
// M115 is used by OpenPnP for detecting the vacuum pump controller

void m_code(int m) {
  switch (m) {
  case 115: // M115 detect firmware
    Serial.println("FIRMWARE_NAME:vacuum pump SOURCE_CODE_URL: https://github.com/koendv/vacuum-pump-controller");
    break;
  case 800: // M800, M801 no-op
  case 801:
    break;
  case 802: // M802 read absolute pressure sensor0 (air)
    m_pressure(m, 0, false);
    break;
  case 803: // M803 read vacuum sensor0 (air) - always 0
    m_pressure(m, 0, true);
    break;
  case 810: // M810 switch vacuum pump off
    PIDctrl::manual(0);
    break;
  case 811: // M811 switch vacuum pump on
    PIDctrl::automatic();
    break;
  case 812: // M812 read absolute pressure sensor1 (pump)
    m_pressure(m, 1, false);
    break;
  case 813: // M813 read vacuum sensor1 (pump)
    m_pressure(m, 1, true);
    break;
  case 820: // M820 switch nozzle 1 vacuum solenoid off
    motor::setswitch(2, false);
    break;
  case 821: // M821 switch nozzle 1 vacuum solenoid on
    motor::setswitch(2, true);
    break;
  case 822: // M822 read absolute pressure sensor2 (nozzle1)
    m_pressure(m, 2, false);
    break;
  case 823: // M823 read vacuum sensor2 (nozzle1)
    m_pressure(m, 2, true);
    break;
  case 830: // M830 switch nozzle 2 vacuum solenoid off
    motor::setswitch(3, false);
    break;
  case 831: // M831 switch nozzle 2 vacuum solenoid on
    motor::setswitch(3, true);
    break;
  case 832: // M832 read absolute pressure sensor3 (nozzle2)
    m_pressure(m, 3, false);
    break;
  case 833: // M833 read vacuum sensor3 (nozzle2)
    m_pressure(m, 3, true);
    break;
  default:
    Serial.print("echo:unknown command \"");
    Serial.print(cmdline);
    Serial.println('"');
    ok = ERR_SYNTAX;
    break;
  }
  return;
}

void printHelp() {
  Serial.println("commands, ## = int, #.## = float:");
  Serial.println("? print status");
  Serial.println("s#.## setpoint");
  Serial.println("p#.## proportional gain");
  Serial.println("i#.## integral gain");
  Serial.println("d#.## derivative gain");
  Serial.println("o#.## manual mode");
  Serial.println("a autotune");
  Serial.println("l## logging on/off");
  Serial.println("m## m-code");
  Serial.println("v## valve on/off");
  Serial.println("w write settings");
  Serial.println("r reset");
  Serial.println("f firmware");
  Serial.println("h help");
}

void printStatus() {

  Serial.print("vacuum hPa: ");
  Serial.print(sensor::vacuum);
  Serial.print(" motor: ");
  Serial.print(motor::pwma_percent);
  Serial.print("% mode: ");
  if (PIDctrl::isAuto())
    Serial.println("auto");
  else
    Serial.println("manual");

  Serial.print("setpoint hPa: ");
  Serial.print(settings::setpoint);
  Serial.print(" Kp: ");
  Serial.print(settings::Kp);
  Serial.print(" Ki: ");
  Serial.print(settings::Ki);
  Serial.print(" Kd: ");
  Serial.print(settings::Kd);
  Serial.print(" logging: ");
  Serial.println(settings::logging);

  Serial.print("pressure hPa: ");
  for (int i = 0; i < NUM_SENSOR; i++) {
    Serial.print(sensor::fpressure[i]);
    Serial.print(' ');
  }
  Serial.println();
  sensor::printSensors();
}

// print useful firmware info
void printFirmware() {
  Serial.println("compiled " __DATE__); // print firmware version. helpful for support.
  uptime::print();                      // print system uptime
  Serial.print(bytes_free());           // print free ram. helpful for detecting memory leaks.
  Serial.println(" bytes free");
  Serial.print(loopstats::slowest_loop()); // time of slowest loop(), in ms
  Serial.println(" ms slowest loop");
}

void setValve(int i) {
  switch (i) {
  case 00:
    motor::setswitch(2, false); // v00: TB6612 pin B01 off
    break;
  case 01:
    motor::setswitch(2, true); // v01: TB6612 pin B01 on
    break;
  case 10:
    motor::setswitch(3, false); // v10: TB6612 pin B02 off
    break;
  case 11:
    motor::setswitch(3, true); // v11: TB6612 pin B02 on
    break;
  default:
    ok = ERR_VALUE;
    break;
  }
}

/*
   *  Execute command. Commands are a single character,
   *  optionally followed by a float or an int.
   */
void doCommand() {
  double fval = 0;
  int ival = 0;
  ok = ERR_OK;
  cmdline.trim();
  // check numeric argument
  if (cmdline.length() >= 2) {
    if (isDigit(cmdline[1])) {
      fval = cmdline.substring(1).toDouble();
      ival = cmdline.substring(1).toInt();
    } else
      cmdline[0] = ':'; // cause syntax error
  }

  // execute command
  if (echo_on)
    Serial.println();
  if (cmdline.length() != 0) {
    switch (cmdline[0]) {
    case 'p': // set proportional gain
      settings::Kp = fval;
      PIDctrl::reload();
      break;
    case 'i': // set integral gain
      settings::Ki = fval;
      PIDctrl::reload();
      break;
    case 'd': // set derivative gain
      settings::Kd = fval;
      PIDctrl::reload();
      break;
    case 's': // set setpoint
      settings::setpoint = fval;
      PIDctrl::reload();
      break;
    case 'o': // output manual mode
      if (cmdline.length() == 1)
        PIDctrl::automatic();
      else if ((fval >= 0) && (fval <= 100))
        PIDctrl::manual(fval / 100.0 * MAXPWM);
      else
        ok = ERR_VALUE;
      break;
    case 'a': // tune
      autotune::tune();
      loopstats::slowest_loop(); // reset cpu stats
      break;
    case 'l': // console pressure logging on/off
      settings::logging = (ival != 0);
      break;
    case 'v': // switch output pin on/off
      setValve(ival);
      break;
    case 'm': // openpnp.org m-codes
      m_code(ival);
      break;
    case 'w': // write settings to non-volatile
      settings::write();
      break;
    case 'r':  // reset sensors and pid controller
      reset(); // does not return
      break;
    case '?': // print all variables and settings
      printStatus();
      break;
    case 'f':
      printFirmware();
      break;
    case 'h': // help
      printHelp();
      break;
    default:
      ok = ERR_SYNTAX;
      break;
    }
  }
  if (ok == ERR_SYNTAX) {
    Serial.println("what?");
  } else if (ok == ERR_VALUE) {
    Serial.println("how?");
  }
  cmdline = "";
  Serial.println("ok");
  if (echo_on)
    Serial.print(">");
  return;
}

void setup() {
  cmdline.reserve(MAXCMDLEN);
  Serial.begin(115200);
  // wait up to 1 second for usb serial to connect
  for (int i = 0; i < 100; i++)
    if (Serial)
      break;
    else
      delay(10);
  Serial.println();
  Serial.println("vacuum pump - type h for help");
}

void loop() {
  while (Serial.available()) {
    char ch = Serial.read();
    if (isUpperCase(ch))
      ch = ch - 'A' + 'a';
    switch (ch) {
    case '\b':
      if (cmdline.length() > 0) {
        cmdline.remove(cmdline.length() - 1);
        if (echo_on)
          Serial.print("\b \b");
      }
      break;
    case '\r':
    case '\n':
      doCommand();
      break;
    default:
      if (cmdline.length() != MAXCMDLEN)
        cmdline += ch;
      if (ch == 'm')
        echo_on = false; // don't echo m-code
      else if (!isDigit(ch))
        echo_on = true; // echo interactive command
      if (echo_on)
        Serial.print(ch);
      break;
    }
  }
}
} // namespace console

// not truncated

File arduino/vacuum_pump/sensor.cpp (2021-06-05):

#include "sensor.h"
#include "motor.h"
#include "settings.h"
#include <math.h>

#include "breathing_led.h"

// uncomment one and only one of these two includes, to compile for BMP280 or BME280
#include <Adafruit_BMP280.h>
//#include <Adafruit_BME280.h>

//#define SIMULATION

// Chip selects for the four BMP280 headers
#define H1_CS PB12
#define H2_CS PA8
#define H3_CS PB11
#define H4_CS PB10

// pins for SPI bus 1
#define SCK1 PA5
#define MOSI1 PA7
#define MISO1 PA6

// pins for SPI bus 2
#define SCK2 PB13
#define MOSI2 PB15
#define MISO2 PB14

// pins for SPI bus 3
#define SCK3 PB3
#define MOSI3 PB5
#define MISO3 PB4

namespace sensor {
double vacuum;
uint32_t lastMillis = 0;
uint32_t sampleTime = 100;
int ipressure[NUM_SENSOR];
double fpressure[NUM_SENSOR];
const int8_t cs[NUM_SENSOR] = {H1_CS, H2_CS, H3_CS, H4_CS};
uint8_t sensor_id[NUM_SENSOR] = {0};

SPIClass SPITwo(MOSI2, MISO2, SCK2);
//SPIClass SPIThree(MOSI3, MISO3, SCK3);      // hardware SPI3 on STM32F411

// array of sensor chips
#ifdef __BMP280_H__
Adafruit_BMP280 sensor[NUM_SENSOR]{
    Adafruit_BMP280(H1_CS, &SPITwo),            // hardware SPI2
    Adafruit_BMP280(H2_CS, &SPITwo),            // hardware SPI2
    Adafruit_BMP280(H3_CS, MOSI3, MISO3, SCK3), // software SPI3 on STM32F103
    Adafruit_BMP280(H4_CS, MOSI3, MISO3, SCK3)  // software SPI3 on STM32F103
};
#endif

#ifdef __BME280_H__
Adafruit_BME280 sensor[NUM_SENSOR]{
    Adafruit_BME280(H1_CS, &SPITwo),            // hardware SPI2
    Adafruit_BME280(H2_CS, &SPITwo),            // hardware SPI2
    Adafruit_BME280(H3_CS, MOSI3, MISO3, SCK3), // software SPI3 on STM32F103
    Adafruit_BME280(H4_CS, MOSI3, MISO3, SCK3)  // software SPI3 on STM32F103
};
#endif

/*
   * Sensor states:
   * NO_SENSOR  no sensor detected
   * SENSOR_OK  sensor detected and running
   * SENSOR_ERR sensor not responsive.
   *
   * Detect sensor by switching sensor chip select to INPUT_PULLDOWN;
   * CS will be high if sensor present.
   *
   * Detect sensor hung or removed by reading sensorID().
   *
   */

state_enum state[NUM_SENSOR];

void setSampleTime(uint32_t millis) {
  if (millis > 0)
    sampleTime = millis;
}

// logging.
// logs time, motor pwm, pressure in Pa, and checksum in csv format.
// checksum is simple 32-bit sum of timestamp, pressures and motor pwm.

void logSensors(uint32_t now) {
  Serial.print(';');
  uint32_t checksum = 0;
  Serial.print(now);
  Serial.print(';');
  checksum = now;
  Serial.print(motor::pwma);
  Serial.print(';');
  checksum += motor::pwma;
  for (int i = 0; i < NUM_SENSOR; i++) {
    Serial.print(ipressure[i]);
    Serial.print(';');
    checksum += ipressure[i];
  }
  Serial.println(checksum);
}

void printSensors() {
  const static char *msg[] = {"- ", "ok ", "? "};
  Serial.print("sensors ");
  for (int i = 0; i < NUM_SENSOR; i++) {
    uint8_t s = state[i];
    if ((s < 0) || (s > SENSOR_ERR))
      s = SENSOR_ERR;
    Serial.print(msg[s]);
    Serial.print(' ');
  }
  Serial.println();
}

void detectSensor(uint8_t i) {
  state[i] = NO_SENSOR;
  ipressure[i] = 0;
  fpressure[i] = 0.0;
  // detect sensor by reading cs pin - sensor pulls cs up
  pinMode(cs[i], INPUT_PULLDOWN);
  delay(10); // allow cs to settle
  bool detected = digitalRead(cs[i]);
  if (!detected)
    return;
  if (sensor[i].begin()) {
    sensor_id[i] = sensor[i].sensorID();
    state[i] = SENSOR_OK;
  } else { // unknown sensor type
    pinMode(cs[i], INPUT_PULLDOWN);
    breathingLed::blink(); // blink rapidly
    state[i] = SENSOR_ERR;
  }
}

void detectSensors() {
  for (int i = 0; i < NUM_SENSOR; i++) {
    detectSensor(i);
  }
}

#ifdef SIMULATION

/* simulate sensor and vacuum vessel */
void readSensors() {
  static uint32_t lastSensorMillis = 0;
  uint32_t now = millis();
  float delta_t = (now - lastSensorMillis) / 1000;
  lastSensorMillis = now;

  double motor = 0.0, valve = 0.0;
  const double deadZone = MAXPWM / 5.0; // pump does not turn if voltage too low
  if (motor::pwma > deadZone)
    motor = (motor::pwma - deadZone) / (MAXPWM - deadZone);
  valve = motor::getswitch(2);
  double steadystate = motor * 1000 - valve * 500;
  if (steadystate < 0.0)
    steadystate = 0.0;

  for (int i = 0; i < NUM_SENSOR; i++)
    pressure[i] = 0.0;
  vacuum = vacuum + (steadystate - vacuum) / 40.0;
}

#else

void readSensor(int i) {
  sensors_event_t pressure_event;
  bool detected;
  int count;
  switch (state[i]) {
  case NO_SENSOR:
    // check if sensor plugged in
    // assume pinMode(cs[i], INPUT_PULLDOWN)
    detected = digitalRead(cs[i]);
    if (detected) {
      detectSensor(i);
      if (state[i] != NO_SENSOR)
        printSensors();
    }
    break;
  case SENSOR_OK:
    // read pressure
    if (sensor[i].sensorID() == sensor_id[i]) {
      // getPressureSensor has a resolution of 1 hPa
      // readPressure has a resolution of 0.01 hPa, so we'll use that - smoother regulation
      // sensor accuracy is 0.12 hPa
      ipressure[i] = sensor[i].readPressure();
      fpressure[i] = ipressure[i] / 100.0; // in hPa
    } else {
      ipressure[i] = 0;
      fpressure[i] = 0;
      breathingLed::blink(); // blink rapidly
      pinMode(cs[i], INPUT_PULLDOWN);
      state[i] = SENSOR_ERR;
      printSensors();
    }
    break;
  case SENSOR_ERR:
    // wait until sensor unplugged
    if (digitalRead(cs[i]))
      break;
    state[i] = NO_SENSOR;
    // stop blinking rapidly if no sensors in error state
    count = 0;
    for (int i = 0; i < NUM_SENSOR; i++) {
      if (state[i] == SENSOR_ERR)
        count++;
    }
    if (count == 0)
      breathingLed::blink(224, 5000); // stop blinking rapidly
    printSensors();
    break;

  default:
    // should never happen
    Serial.print("state? ");
    Serial.println(state[i]);
    pinMode(cs[i], INPUT_PULLDOWN);
    state[i] = NO_SENSOR;
    break;
  }
}

void readSensors() {
  for (int i = 0; i < NUM_SENSOR; i++)
    readSensor(i);
  // fpressure[0]] = atmospheric, fpressure[1] = vacuum vessel
  vacuum = fpressure[0] - fpressure[1];
}
#endif

void setSampleTime(int millis) {
  sampleTime = millis;
}

void setup() {
  detectSensors();
  printSensors();
}

void loop() {
  uint32_t now = millis();
  if ((now < lastMillis) || (now - lastMillis > sampleTime)) {
    readSensors();
    if (settings::logging)
      logSensors(now);
    lastMillis = now;
  }
}
} // namespace sensor

// not truncated

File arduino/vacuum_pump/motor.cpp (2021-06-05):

#include "motor.h"
#include <Arduino.h>

#define TB6612_PWMA PB6
#define TB6612_AIN2 PA2
#define TB6612_AIN1 PA1
#define TB6612_STBY PA0
#define TB6612_PWMB PB7
#define TB6612_BIN1 PB8
#define TB6612_BIN2 PB9

namespace motor {

int pwma, pwmb;
float pwma_percent, pwmb_percent;

void setup() {

  analogWriteFrequency(20000);
  analogWriteResolution(16);

  pinMode(TB6612_STBY, OUTPUT);
  pinMode(TB6612_PWMA, OUTPUT);
  pinMode(TB6612_AIN1, OUTPUT);
  pinMode(TB6612_AIN2, OUTPUT);
  pinMode(TB6612_PWMB, OUTPUT);
  pinMode(TB6612_BIN1, OUTPUT);
  pinMode(TB6612_BIN2, OUTPUT);

  digitalWrite(TB6612_STBY, LOW);
  analogWrite(TB6612_PWMA, MAXPWM);
  digitalWrite(TB6612_AIN1, LOW);
  digitalWrite(TB6612_AIN2, LOW);
  digitalWrite(TB6612_PWMB, HIGH);
  digitalWrite(TB6612_BIN1, LOW);
  digitalWrite(TB6612_BIN2, LOW);
  digitalWrite(TB6612_STBY, HIGH);

  pwma = 0;
  pwmb = 0;
  pwma_percent = 0;
  pwmb_percent = 0;
}

// use up to two brushless DC motors

void speed(int pwm, int port) {
  if (isnan(pwm))
    return;
  if (pwm < MINPWM)
    pwm = MINPWM;
  if (pwm > MAXPWM)
    pwm = MAXPWM;

  if (port == 0) { // port A
    pwma = pwm;
    pwma_percent = pwma * 100.0 / MAXPWM;
    if (pwm == 0) {
      digitalWrite(TB6612_AIN1, LOW);
      digitalWrite(TB6612_AIN2, LOW);
      analogWrite(TB6612_PWMA, pwm);
    } else if (pwm > 0) {
      digitalWrite(TB6612_AIN1, HIGH);
      digitalWrite(TB6612_AIN2, LOW);
      analogWrite(TB6612_PWMA, pwm);
    } else {
      digitalWrite(TB6612_AIN1, LOW);
      digitalWrite(TB6612_AIN2, HIGH);
      analogWrite(TB6612_PWMA, -pwm);
    }
  } else { // port B
    pwmb = pwm;
    pwmb_percent = pwmb * 100.0 / MAXPWM;
    if (pwm == 0) {
      digitalWrite(TB6612_BIN1, LOW);
      digitalWrite(TB6612_BIN2, LOW);
      analogWrite(TB6612_PWMB, pwm);
    } else if (pwm > 0) {
      digitalWrite(TB6612_BIN1, HIGH);
      digitalWrite(TB6612_BIN2, LOW);
      analogWrite(TB6612_PWMB, pwm);
    } else {
      digitalWrite(TB6612_BIN1, LOW);
      digitalWrite(TB6612_BIN2, HIGH);
      analogWrite(TB6612_PWMB, -pwm);
    }
  }
}

// use up to four on/off switches
// note:
// - AOUT1 and AOUT2 can not be powered at the same time.
// - BOUT1 and BOUT2 can not be powered at the same time.
// this is because we are using a dc motor driver ic, and
// a motor can go forward or backward, but not both at the same time.
// see TB6612 datasheet, p.4, H-SW Control Function

void setswitch(int nr, bool onoff) {
  if (onoff) {
    // before switching on a solenoid, switch off the other solenoid of the pair
    switch (nr) {
    case 0:
      digitalWrite(TB6612_PWMA, HIGH);
      digitalWrite(TB6612_AIN2, false);
      digitalWrite(TB6612_AIN1, true);
      break;
    case 1:
      digitalWrite(TB6612_PWMA, HIGH);
      digitalWrite(TB6612_AIN1, false);
      digitalWrite(TB6612_AIN2, true);
      break;
    case 2:
      digitalWrite(TB6612_PWMB, HIGH);
      digitalWrite(TB6612_BIN2, false);
      digitalWrite(TB6612_BIN1, true);
      break;
    case 3:
      digitalWrite(TB6612_PWMB, HIGH);
      digitalWrite(TB6612_BIN1, false);
      digitalWrite(TB6612_BIN2, true);
      break;
    default:
      break;
    }
  } else {
    switch (nr) {
    case 0:
      digitalWrite(TB6612_PWMA, HIGH);
      digitalWrite(TB6612_AIN1, false);
      break;
    case 1:
      digitalWrite(TB6612_PWMA, HIGH);
      digitalWrite(TB6612_AIN2, false);
      break;
    case 2:
      digitalWrite(TB6612_PWMB, HIGH);
      digitalWrite(TB6612_BIN1, false);
      break;
    case 3:
      digitalWrite(TB6612_PWMB, HIGH);
      digitalWrite(TB6612_BIN2, false);
      break;
    default:
      break;
    }
  }
}

bool getswitch(int nr) {
  bool retval = false;
  switch (nr) {
  case 0:
    retval = digitalRead(TB6612_AIN1);
    break;
  case 1:
    retval = digitalRead(TB6612_AIN2);
    break;
  case 2:
    retval = digitalRead(TB6612_BIN1);
    break;
  case 3:
    retval = digitalRead(TB6612_BIN2);
    break;
  default:
    break;
  }
  return retval;
}
} // namespace motor

// not truncated

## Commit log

2021-05-26 pressure sensor
    [pressure_sensor.scad, pressure_sensor.stl, pressure_sensor_lid.stl]
2021-05-30 print screen
2021-06-13 motor pwm input
